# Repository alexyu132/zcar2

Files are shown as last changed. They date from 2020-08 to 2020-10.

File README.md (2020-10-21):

# zcar2

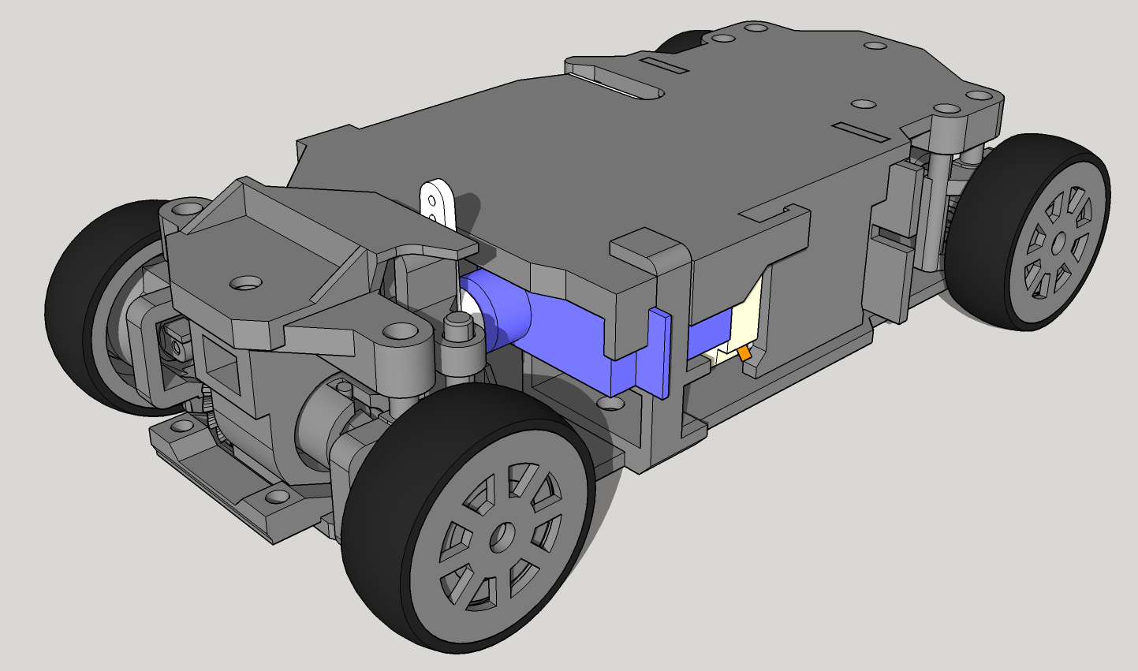
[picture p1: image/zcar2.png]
zcar2 image


A nearly fully 3D-printed, 4WD RC drift car. 1:28 scale, fits 90mm (M) wheelbase MINI-Z shells*.

\*Note: The front section of the chassis is relatively tall and won't fit certain shells, such as the RX-7 FD. Verified compatible with the AE86 shell.
Test drive: https://youtu.be/90DoZpYbfy4

U-joint closeup: https://youtu.be/g_EzM2HMQvg

Some parts in this design are quite challenging to print - make sure you have a well-calibrated printer before attempting.

Features:
- Fully indepdendent sliding suspension
- 4WD drivetrain with printed U-joints (no differentials)
- Mid-mounted battery and motor - approx 50-50 weight distribution
- Parallel steering geometry for drifting
- Uses common M3 fasteners, locknuts everywhere
- TPU printed tires

## Non-printed Parts

|  Part | Quantity | Notes  |
|---|---|---|
|  M3x10mm button head screw | 8  | |
|  M3x8mm button head screw | 7 | |
|  M3x12mm button head screw | 1  | |
|  M3x18mm button head screw | 1  | |
|  M3 lock nut | 17 | |
| MR105 bearing | 8 | |
| 130 size brushed motor, 2s compatible | 1 | |
| GH-S37D 3.7g servo | 1 |  |
| Compression spring, ~4mm OD, ~4mm length | 4 | Softer springs are better.  Springs from multicolor retractable pens work well here when cut to length. Ordinary pen springs are too stiff. |
| Venom Fly 300mah 2S battery | 1 | |
| Small brushed ESC, 2S compatible | 1 |
| Small radio receiver | 1 | 2 channels or more. Flysky GR3E works if you remove its case. |
| MINI-Z shell, M wheelbase | 1 | Tested with Kyosho MZQ101 AE86 shell |

## Assembly
Todo

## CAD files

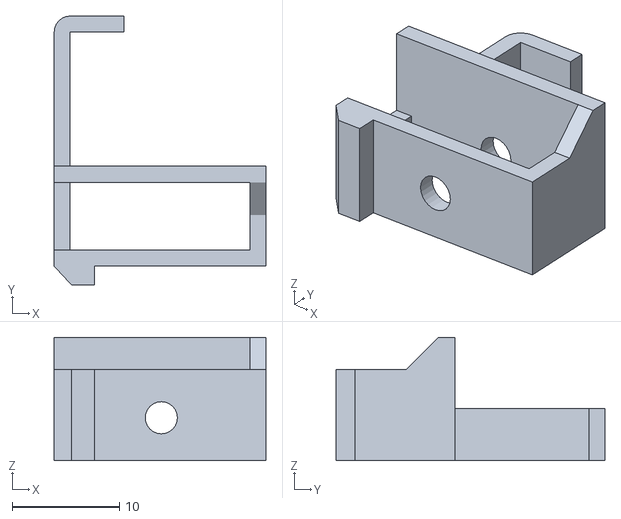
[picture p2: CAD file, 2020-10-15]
stl/servo support.stl
19.8 x 25.1 x 11.5

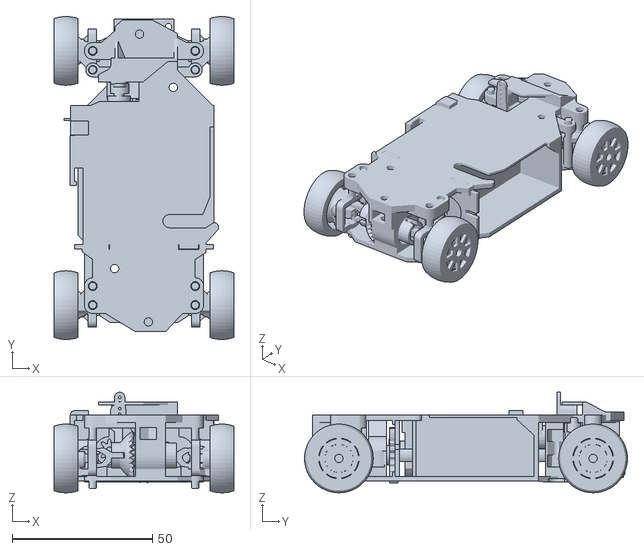
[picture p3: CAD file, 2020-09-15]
zcar2.stl
64.0 x 115.0 x 35.9

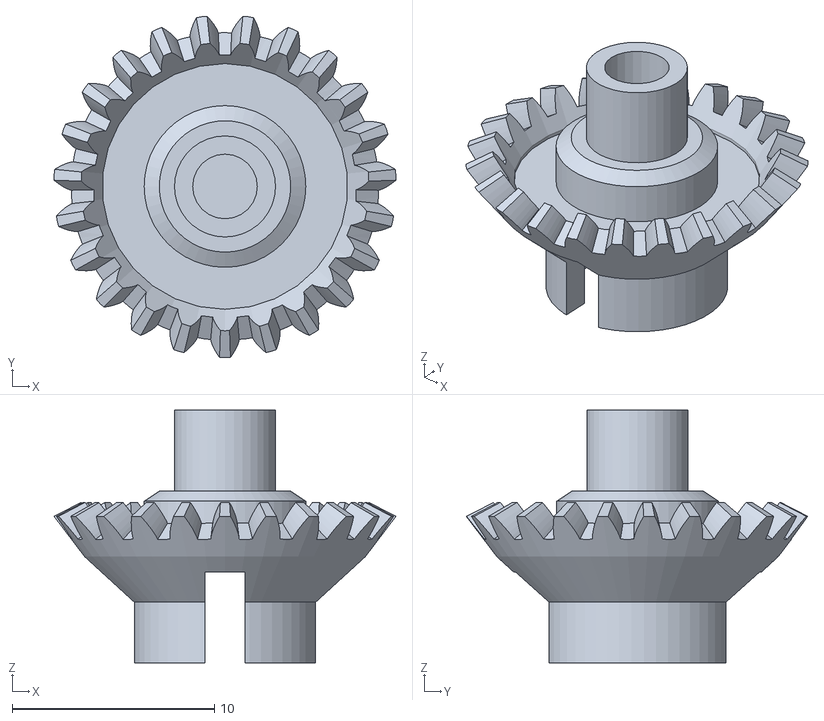
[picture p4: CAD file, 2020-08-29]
stl/axle bevel gear (print 2).stl
16.9 x 16.9 x 12.5

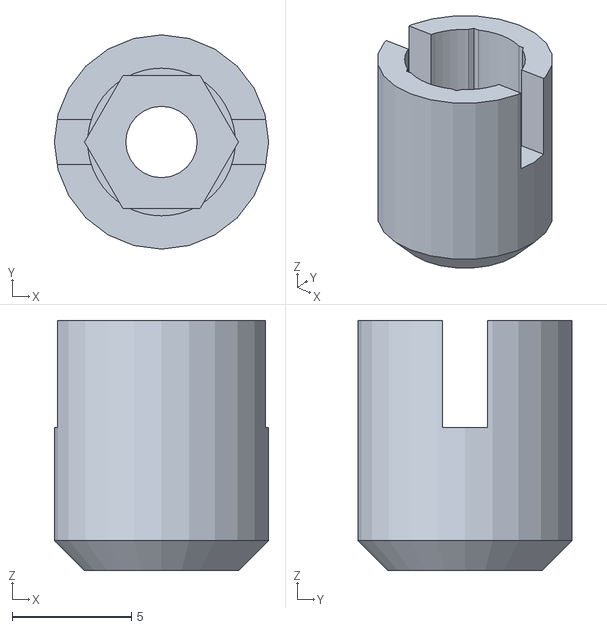
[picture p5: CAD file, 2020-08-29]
stl/axle dogbone cup (print 2).stl
9.00 x 9.00 x 10.5

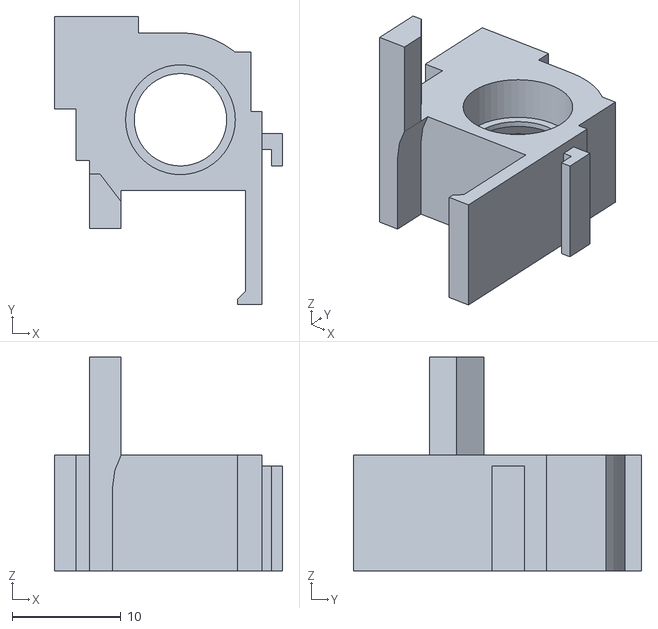
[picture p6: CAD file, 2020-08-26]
stl/axle bearing block front.stl
21.0 x 26.5 x 19.7

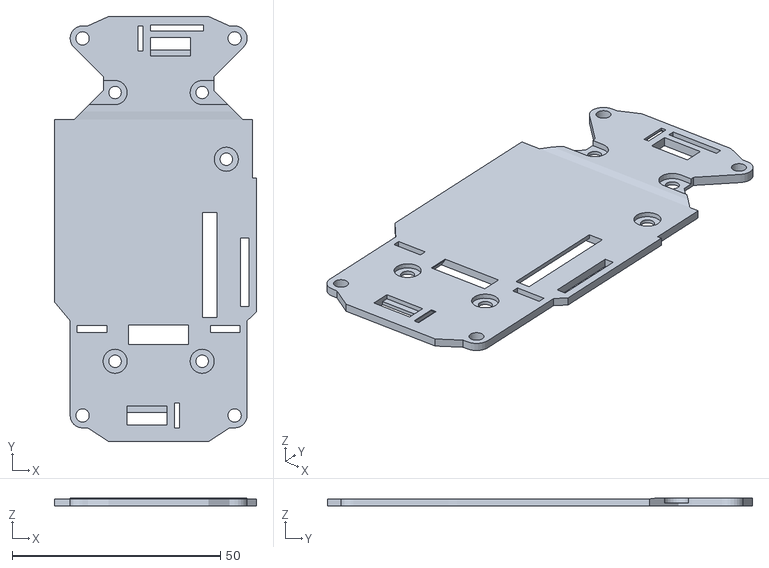
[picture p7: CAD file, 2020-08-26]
stl/chassis bottom plate.stl
48.5 x 102.0 x 2.00

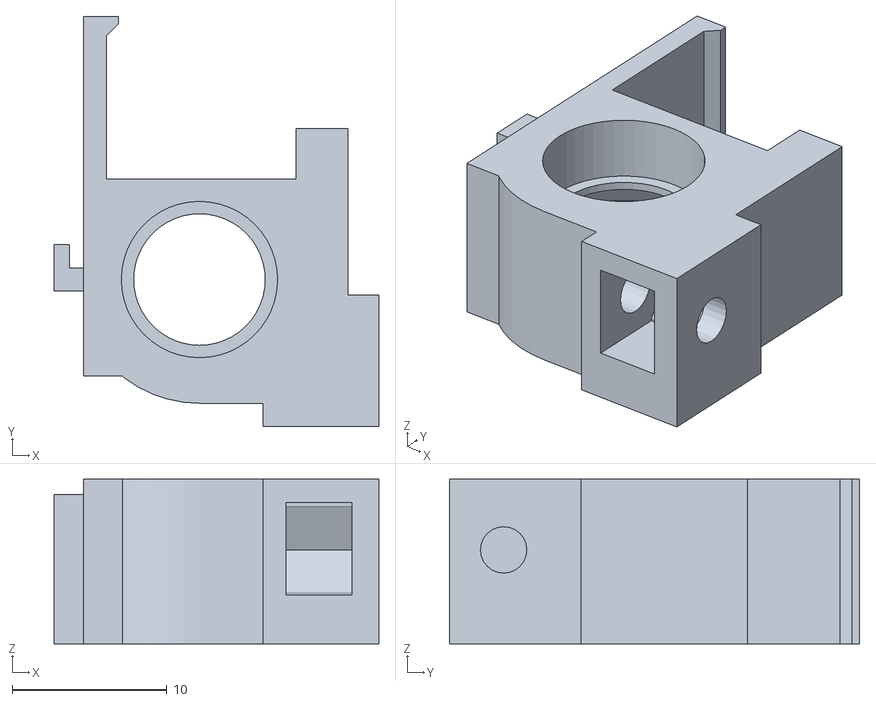
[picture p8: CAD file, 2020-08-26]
stl/axle bearing block rear.stl
21.0 x 26.5 x 10.6

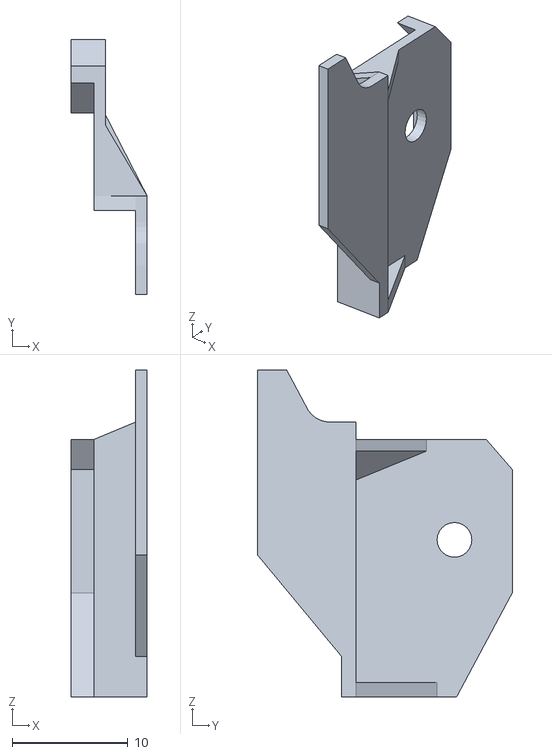
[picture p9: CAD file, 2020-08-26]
stl/steering rack retaining bracket.stl
6.60 x 22.0 x 28.2

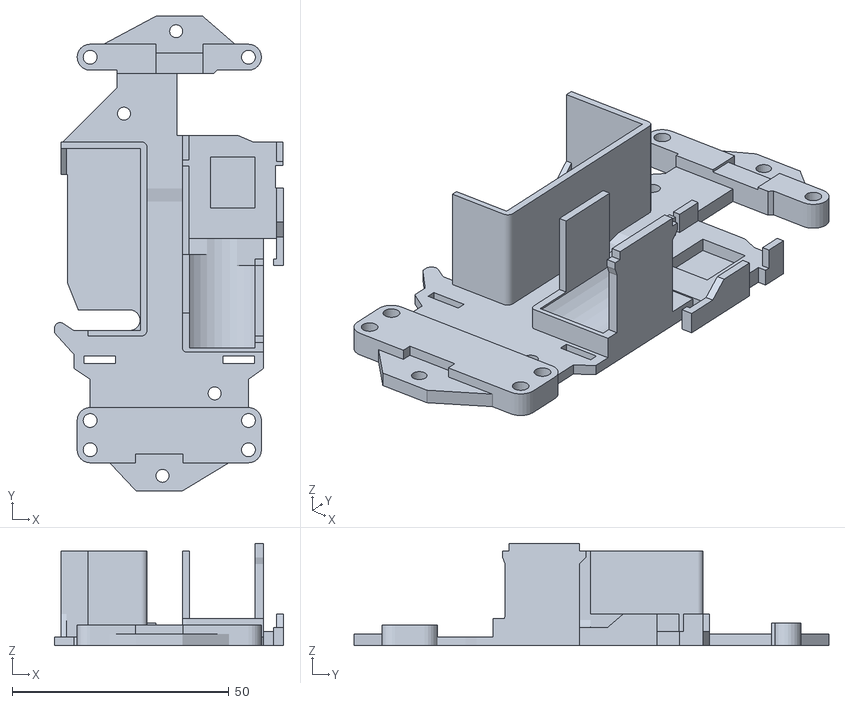
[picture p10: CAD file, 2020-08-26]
stl/chassis top plate.stl
52.9 x 109.5 x 23.6

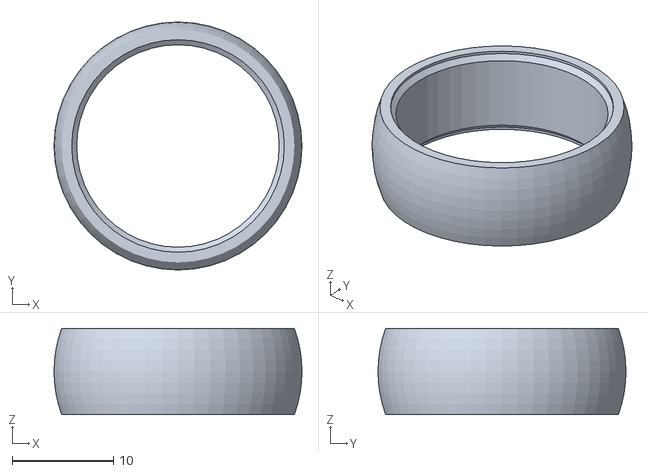
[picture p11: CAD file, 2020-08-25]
stl/tire (print 4).stl
24.5 x 24.5 x 8.50

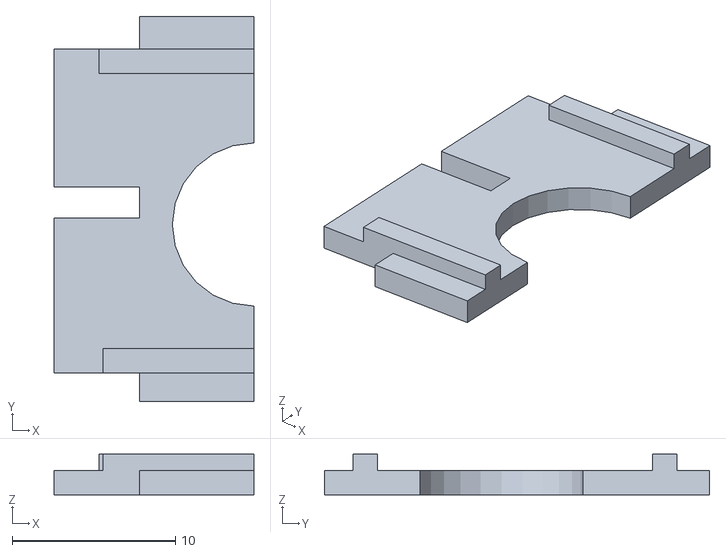
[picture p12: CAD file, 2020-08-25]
stl/rear body mount left.stl
12.2 x 23.6 x 2.50

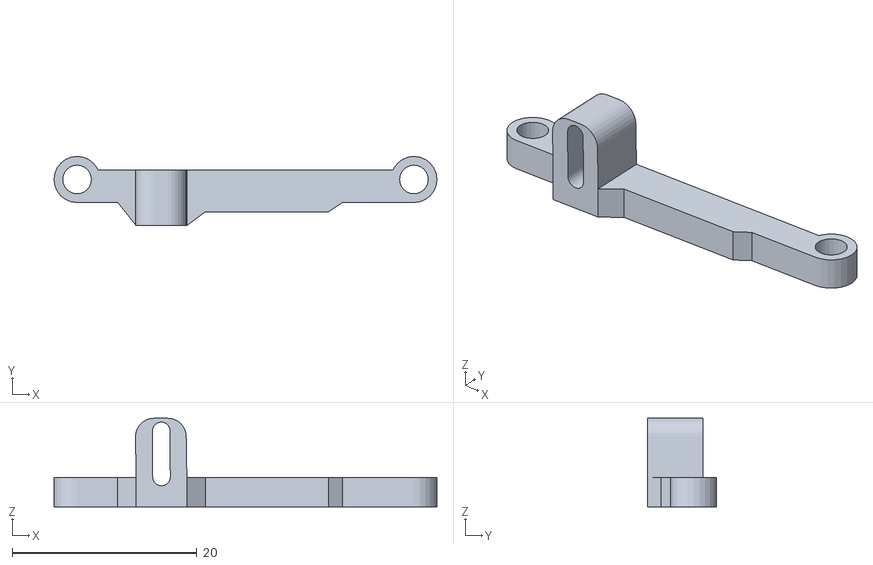
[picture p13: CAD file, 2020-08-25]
stl/steering rack.stl
41.5 x 7.50 x 9.60

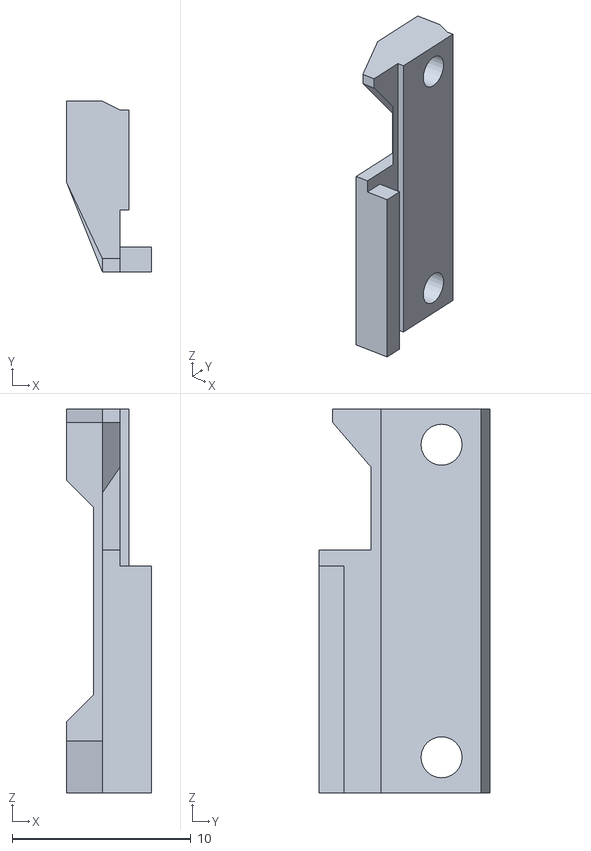
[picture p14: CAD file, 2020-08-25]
stl/front body mount.stl
4.75 x 9.55 x 21.5

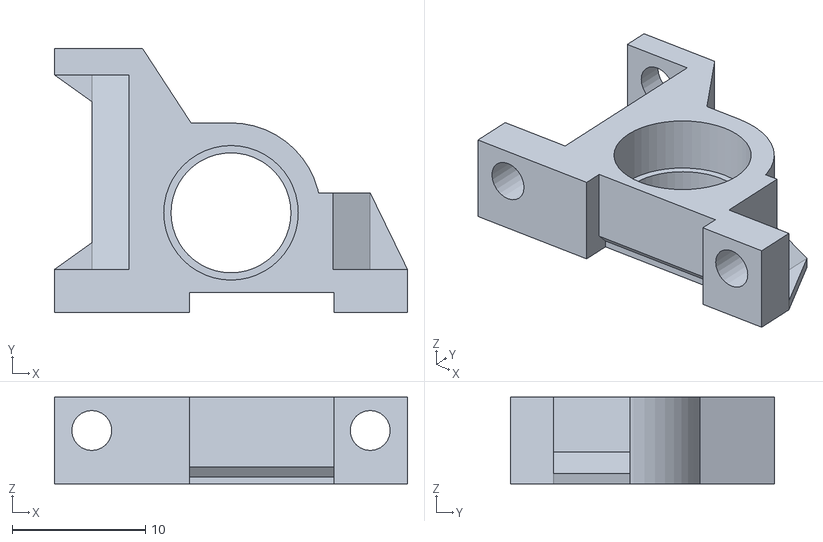
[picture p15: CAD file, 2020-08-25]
stl/driveshaft bearing block rear.stl
26.5 x 19.8 x 6.50

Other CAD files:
stl/rear body mount right.stl
stl/u-joint end (print 4).stl
stl/u-joint shaft (print 4).stl
stl/driveshaft.stl
stl/driveshaft bearing block front.stl
stl/driveshaft bevel gear (print 2).stl
stl/driveshaft spur.stl
stl/motor pinion.stl
stl/u-joint coupler (print 4).stl
stl/wheel (print 4).stl
stl/wheel bearing block 1 (print 2).stl
stl/wheel bearing block 2 (print 2).stl
zcar2.skp

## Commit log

2020-07-24 steering knuckle
    [cvtest.skp]
2020-07-24 tweak steering knuckle
    [cvtest.skp]
2020-07-24 strengthen knuckle
    [cvtest.skp]
2020-07-24 suspension c frame
    [cvtest.skp]
2020-07-24 suspension links
    [cvtest.skp]
2020-07-25 begin steering
    [cvtest.skp]
2020-07-25 steering rack, align parts
    [cvtest.skp]
2020-07-25 add servo
    [cvtest.skp]
2020-07-25 begin center bearing mount
    [cvtest.skp]
2020-07-25 steering rack
    [cvtest.skp]
2020-07-25 begin new suspension top mount
    [cvtest.skp]
2020-07-26 begin attaching things together
    [cvtest.skp]
2020-08-06 revert to non wishbone suspension
    [cvtest.skp]
2020-08-06 top plate, begin rear
    [cvtest.skp]
2020-08-06 begin motor and servo mountings
    [cvtest.skp]
2020-08-06 fnish motor and servo mounts
    [cvtest.skp]
2020-08-07 battery mount
    [cvtest.skp]
2020-08-07 rear body mount
    [cvtest.skp]
2020-08-07 initial design complete
    [cvtest.skp]
2020-08-07 small tweaks and fixes
    [cvtest.skp]
2020-08-09 various improvements and fixes
    [cvtest.skp]
2020-08-09 printability tweaks
    [cvtest.skp]
2020-08-09 steering rack top guide, misc fixes
    [cvtest.skp]
2020-08-11 strengthen wheel bearing mounts and increase bed contact area
    [cvtest.skp]
2020-08-12 adjust clearances, widen end bearing blocks
    [cvtest.skp]
2020-08-12 test reinforced and narrowed wheel bearing blocks
    [cvtest.skp]
2020-08-12 narrow track width by 0.75mm
    [cvtest.skp]
2020-08-12 add new tire design
    [cvtest.skp]
2020-08-12 adjust clearances
    [cvtest.skp]
2020-08-12 tweaks and fixes
    [cvtest.skp]
2020-08-13 switch sides for servo/motor and battery
    [cvtest.skp]
2020-08-13 add additional top plate connection points to prevent tilt
    [cvtest.skp]
2020-08-13 reduce steering assembly height
    [cvtest.skp]
2020-08-15 increase pitch of motor gear pair
    [cvtest.skp]
2020-08-15 increase suspension pin clearance
    [cvtest.skp]
2020-08-15 tweak battery holder
    [cvtest.skp]
2020-08-15 strengthen u-joints, align front pivot points
    [cvtest.skp]
2020-08-15 reduce suspension travel
    [cvtest.skp]
2020-08-15 further u joint strengthening
    [cvtest.skp]
2020-08-15 extend wheelbase by 0.5mm
    [cvtest.skp]
2020-08-17 add/tweak cable guides, slight steering arm adjustment
    [cvtest.skp]
2020-08-18 bit more u joint strengthening
    [cvtest.skp]
2020-08-19 slightly extend u joint links
    [cvtest.skp]
2020-08-19 thicken wheel spokes, adjust motor position
    [cvtest.skp]
2020-08-20 Clean up and rename skp file
    [cvtest.skp, zcar2.skp]
2020-08-20 Add STLs, fix servo support bracket
    [axle bearing block front.stl, axle bearing block rear.stl, axle bevel gear.stl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]
2020-08-20 Adjustments to better match screw lengths
    [driveshaft bearing block rear.stl, driveshaft.stl, zcar2.skp]
2020-08-21 alter slim tire profile
    [zcar2.skp]
2020-08-21 significantly strengthen u-joint ends
    [u-joint end.stl, zcar2.skp]
2020-08-21 Adjust u-joints for ease of assembly
    [u-joint end.stl, u-joint shaft.stl, zcar2.skp]
2020-08-25 Fix BOM screw/nut quantity
2020-08-25 Tighten up suspension pin clearances, rear driveshaft bearing block screw length fix, front body mount tweak
    [chassis bottom plate.stl, chassis top plate.stl, driveshaft bearing block rear.stl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]
2020-08-25 extend lower guide for steering rack
    [axle bearing block front.stl, steering rack.stl, zcar2.skp]
2020-08-25 Add quantities to stl names
    [axle bevel gear (print 2).stl, axle dogbone cup (print 2).stl, driveshaft bevel gear (print 2).stl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]
2020-08-25 make rear body mount tabs flush with top/bottom plates
    [rear body mount left.stl, rear body mount right.stl, zcar2.skp]
2020-08-25 Add image, clean up skp, update tire stl
    [tire (print 4).stl, zcar2.skp]
2020-08-26 Move battery inwards slightly, move axle bearing block screws closer to center
    [axle bearing block front.stl, axle bearing block rear.stl, chassis bottom plate.stl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]
2020-08-27 Extend servo support
    [servo support.stl, zcar2.skp]
2020-08-29 Reinforce axle dogbone screw holes
    [axle bevel gear (print 2).stl, axle dogbone cup (print 2).stl, zcar2.skp]
2020-09-15 Add preview stl
    [zcar2.stl]
2020-10-15 Fix servo support
    [servo support.stl, zcar2.skp]
